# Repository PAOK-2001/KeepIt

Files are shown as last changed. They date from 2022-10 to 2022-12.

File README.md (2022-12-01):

# System Overview

The present system is intended as a demonstrator of how to apply computer vision techniques for autonomous driving. In particular, we tackle the matter of lane detection and following.

To deploy the image processing we will use a _Raspberry Pi 4B_ which will run the OpenCv script that finds the lanes and computes the center; it will also calculate the offset between said center and the center of the camera, returning an error (measured in pixels). The systems for moving and steering the car are controlled by a _Raspberry Pi Pico_, running FreeRTOS. The micro-controller will read the error by I2C and apply a proportional control loop (tunned using the Ziegler-Nichols experimental method) to correct the direction using the steering. 

Current and voltage sensors for a stable functioning of the system; a low-pass filter was implemented to rule out any current peaks and only stop the system when current to the motors consistently rises as a result of motor stall.

The system is summarized in the following diagram.

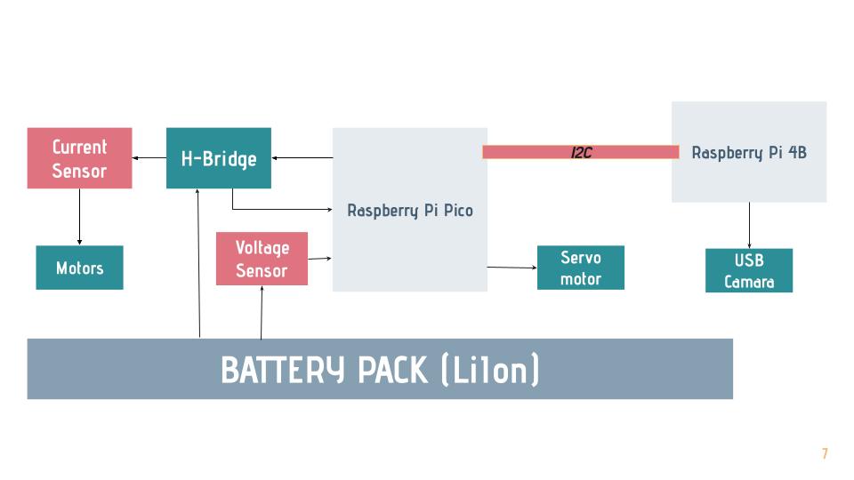
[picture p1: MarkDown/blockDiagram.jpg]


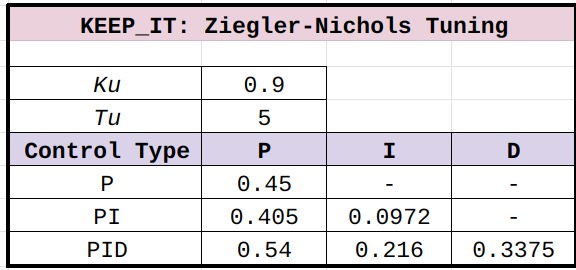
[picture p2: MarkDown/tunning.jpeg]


# Lane Detector
## Methodology
The focus of this project was to create a lane detector class for future implementation in lane keep. The approach for detecting the lanes consisted in finding the edges present in the image using gradient difference (Canny); then masking the image to only include the area corresponding to the road, upon which Hough Transform was applied, detecting probable lines in the image. A linear regression was obtained for each line, which allowed the classification into right (positive slope) and left (negative slope) boundaries; finally, the average coefficients  were found for each boundary, which described the average lines that delimited the lane.  

## Theoretical Background
### Hough Transform
Represents points as lines in Hough space, where the axis represents the values of a linear equation corresponding to a line that goes through that point . In particular, Hough transform uses the polar representation of a line      &rho;= Acos(&theta;)+Bcos(&theta;) where the axes are &rho; and &theta;.

For multiple points, Hough Transform detects the area in Hough space with the
most number of interceptions, returning the most probable values of the linear equation describing the collection of points. In OpenCV this is implemented as HoughLinesP, and returns the cartesian coordinates of the detected line in a vector of 4 integers Vec4i {x1,y1,x2,y1}.

Hough Space HoughTransform

### Canny Edge Detection

Canny is an algorithm that uses various states to detect the edge lines in an image. Firstly it applies a Gaussian Blur to the matrix of pixels to eliminate noise within the image. 
    
Then it uses the Sobel operator to calculate the pixel gradient in all directions. for those gradients Canny’s algorithm looks for those who are bigger than their neighbors, returning a thin edge line. 

## Lane Detector Object

    class laneDetector{
        private:
            // Images states used in lane detection
            Mat edgeImg, lineImg;
            // Lane lines in the format of a 4 integer vector such as  (x1, y1, x2, y2), 
            Vec4i leftLine, rightLine;
            // Coordinate that represents the senter of given lane
            Point center;
            // Auxiliary functions
            static pair<float,float> linearFit(Vec4i lineCoordinates); 
            static float averageCoheficient(vector<float> registeredCoheficients);
            static Vec4i makeCoordinate(float slope, float intercept, int imgHeight);

        public:
            laneDetector();
            void loadFrame(Mat cameraFrame);
            void findLanes();
            void findCenter();
            void display(Mat cameraFrame);
    };
### Class Composition
#### Atributes
| Atribute | Description |
| --- | ----- |
| edgeIMG | Pixel matrix that stores the Canny version of the loaded frame.Canny edgeIMG  |
| lineIMG | Pixel matrix that stores the drawed lines and center point that will blended with the orignal image in the final display. lineIMG edgeIMG |
| leftLine, rightLine | A Vec4i structure that stores the coordinates of the endpoints of the respective lines that delimit the lane. Format: {x1, y1, x2, y2}|
|center|Point object that stores the coordinates for the center of the lanes|
#### Methods
##### Static
|Method| Description  |
| --- | ----- |
|linearFit(Vec4i lineCoordinates)|Takes a vector of 4 integers representing the endpoints of a line and returns the slope and intercept as a pair.|
|averageCoheficient(vector<float> registeredCoheficients)|Takes a vector of coheficients and returns the average value.|
|makeCoordinate(float slope, float intercept, int imgHeight)|Takes the coheficients of a linear equation and the height of the image and calcultates the coordinates of a a line.|
##### Non-Static
|Method| Description  |
| --- | ----- |
|void loadFrame(Mat cameraFrame) | Loads the image where the lanes wish to be found. It applies converts it to grayscale, and applies Canny Edge Detection, storing the result in *edgeIMG*.|
|void findLanes()| It makes mask using polygons to isolate the area where the road is, updating *edgeIMG*. Once the region on interest is obtained Hough Transform is used to detect the lines present; afterwards the **linearFit** method is used to find the slope and intercept for each line. Based on the slope, the lines are categorized into right and left boundaries. Finally, it finds the average lines for each side using **averageCoheficient** and it makes the endpoint coordinates (using **makeCoordinates**) to store them in *rightLine* and *leftLine*. It draws said lines on *lineIMG*|
|void findCenter()|Finds the center of the lane using the coordinates stored in *rightLine* and *leftLine*. Draws the center as a circle in *lineIMG*|
|void display(Mat cameraFrame) | Overlays the *lineIMG* on the real fram captured by the camera. |

# Implementaion
The Lane Detector can be used to find lanes in a single image or a video (read from a file or camera.)

**Still image:**

    laneDetector lanes;
    frame = imread("imageName");
    lanes.loadFrame(frame);
    lanes.findLanes();
    lanes.findCenter();
    lanes.display(frame);

**Camera:**

    VideoCapture dashCam(path);
    for (;;){
        dashCam.read(frame);
        lanes.loadFrame(frame);
        lanes.findLanes();
        lanes.findCenter();
        lanes.display(frame);
        if(waitKey(5)== 27){
            break;
        }
    }

# CAD DESIGN

## Base and Steering

For this project we decided to laser cut a custom base to build the model car upon; we designed it using SolidWorks and leaving the necessary holes for mounting the electrical system. A custom shroud was also built to mount the web cam on the front of the car.

For controlling the direction of the model, we implemented a simplified version of _Ackermann Steering_ which is controlled using a servo motor. 

Finished prototype             | View of Ackermann Steering
:-------------------------:|:-------------------------:
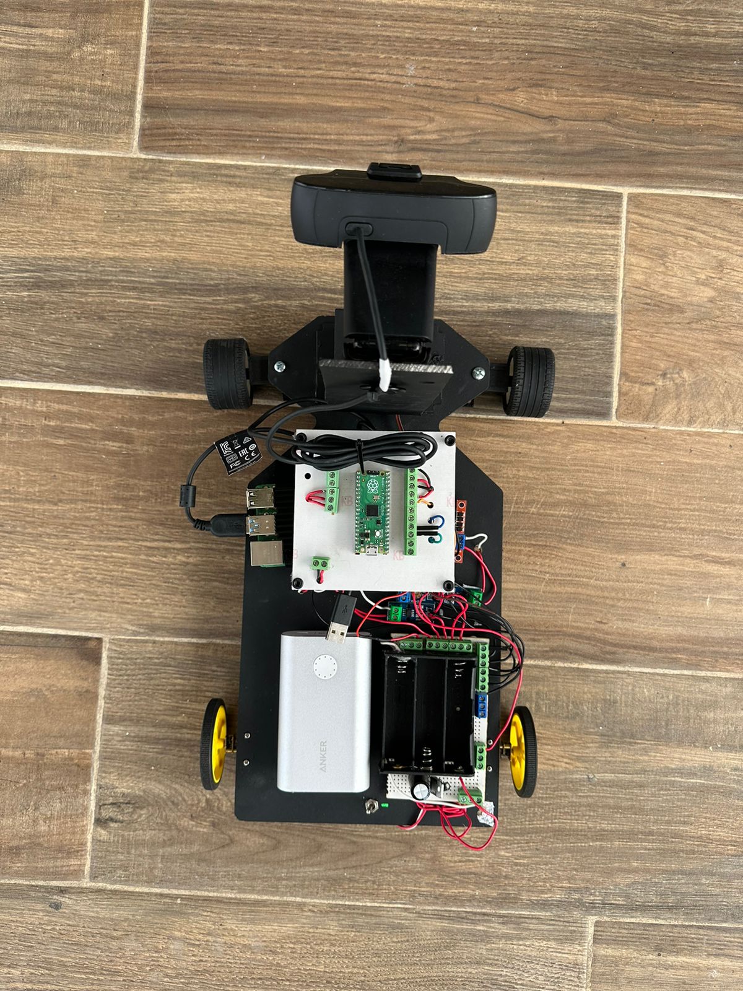
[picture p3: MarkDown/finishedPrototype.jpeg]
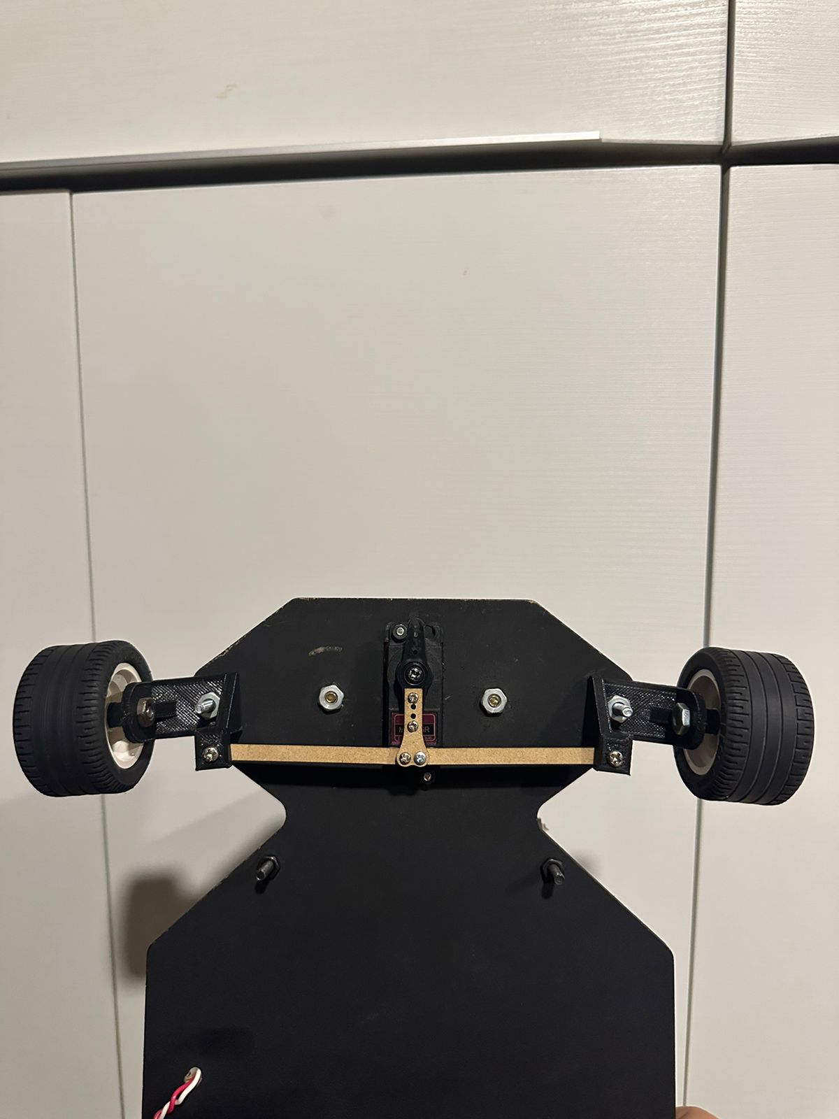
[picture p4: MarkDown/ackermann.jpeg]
  |   

## Electrical

For a secure connection a breakout board was made to map the GPIO pins using screw terminals. A power breakout board was also designed for a 4 cells 18650 BMS; however, due to a faulty BMS it was not used in the final implementation.
GPIO Breakout Board             | BMS Breakout Board
:-------------------------:|:-------------------------:
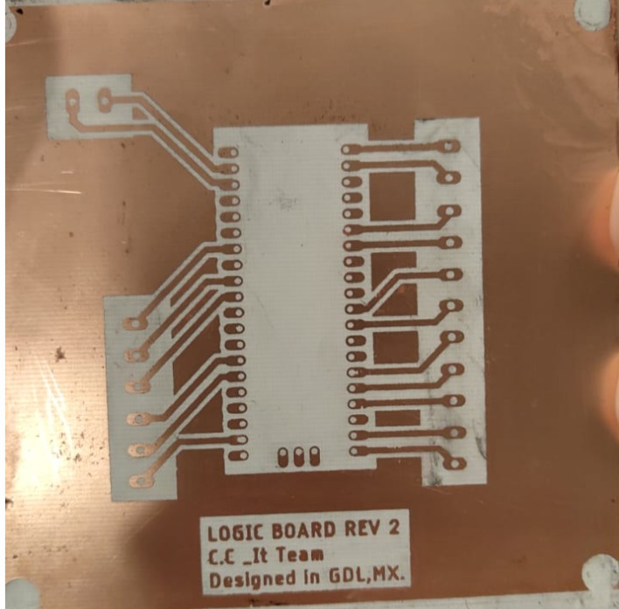
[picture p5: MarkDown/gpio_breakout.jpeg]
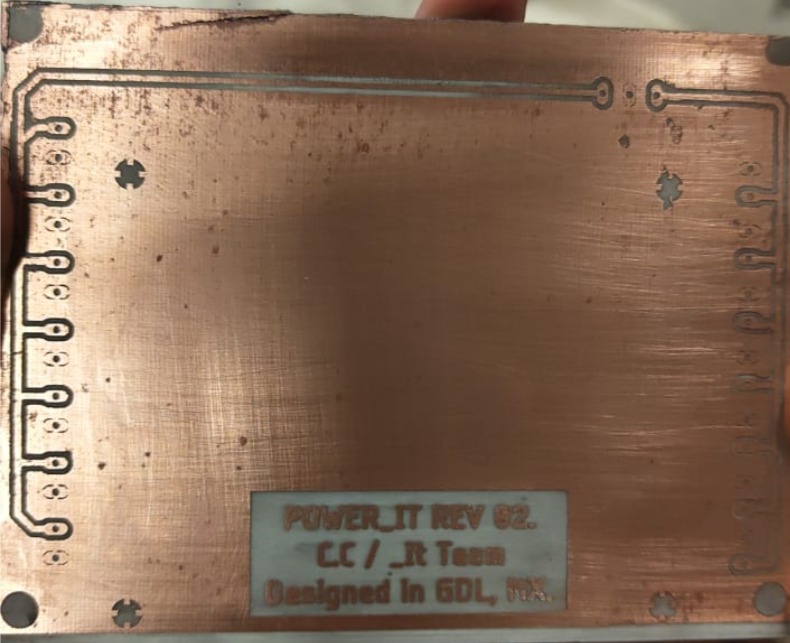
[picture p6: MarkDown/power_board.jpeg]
  |   

### Demo Reel: 

https://www.youtube.com/watch?v=GjENCYGIipA&ab_channel=AbrahamDeAlbaFranco

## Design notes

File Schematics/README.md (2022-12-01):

### Appendix: GPIO Breakout Board
_I2C0_
- GP4 (I2C0_SDA)
- GP5 (I2CO_SCL)

_I2C1_
- GP21 (I2C1_SDA)
- GP20(I2C1_SCL)
_UART COMMUNICATION_ 
- GP0
- GP1

_H-BRIDGE (PWM):_
- Motor1: GP15, GP14
- Motor2: GP13, GP12

_SERVO:_
- GP11

_ALIMENTATION_
- +:  VSYS [40]
- GND: [38]

_VOLTAGE SENSOR (ADC)_
- GP28

_CURRENT SENSORS (ADC)_
- SENSOR1: GP27
- SENSOR2: GP26

_GENERAL PURPOSE_:
- GP8
- G99
- GP17

### POWER

- 5V:  x7
- 3.3V: x7
- 12V: x3
- GND: x7

# Photos

_Acknowlegment:_ Special thanks to [John Corrado (@CorradoCorrado)](https://github.com/CorradoCorrado) for his guidance on the design and manufacturing of the boards!

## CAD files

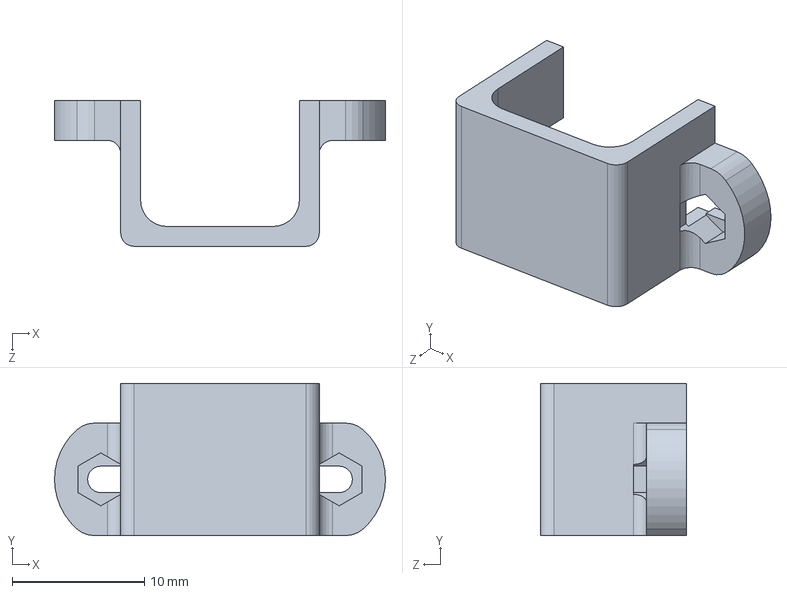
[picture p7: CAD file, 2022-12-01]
Schematics/Chassis_and_direction/Bracket.step.SLDPRT
25.0 x 11.5 x 11.0 mm

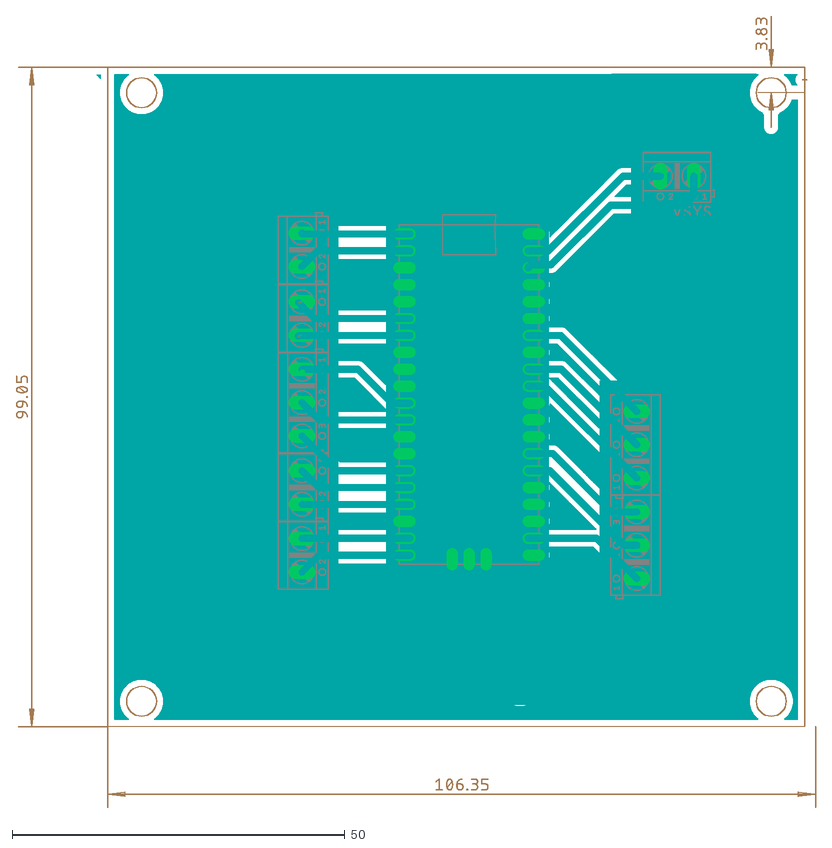
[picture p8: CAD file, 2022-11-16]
Schematics/LogicBoard - Pico/LogicBoard-Pico.dxf
120.2 x 118.9

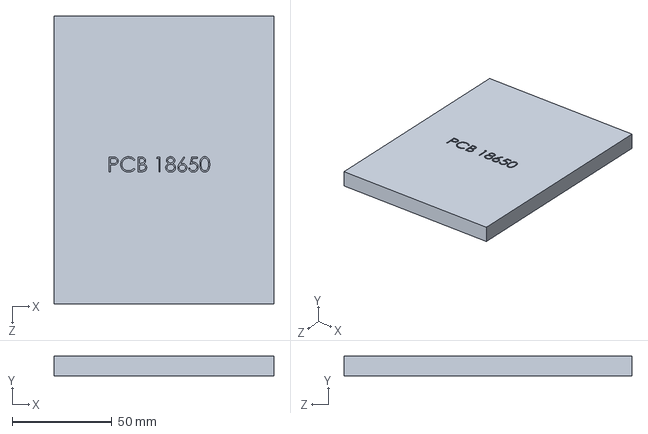
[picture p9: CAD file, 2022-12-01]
Schematics/Chassis_and_direction/bms.SLDPRT
110.0 x 10.0 x 144.0 mm

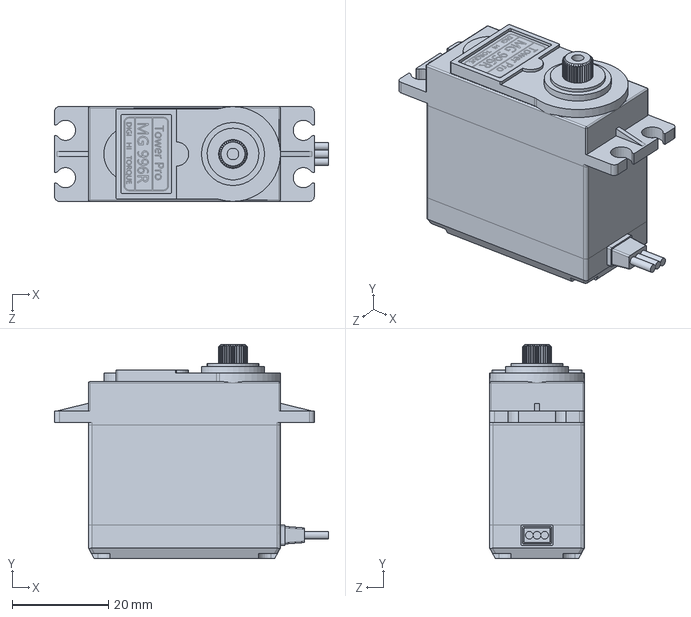
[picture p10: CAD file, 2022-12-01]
Schematics/Chassis_and_direction/Servo Motor MG996R.SLDPRT
57.0 x 44.5 x 19.7 mm

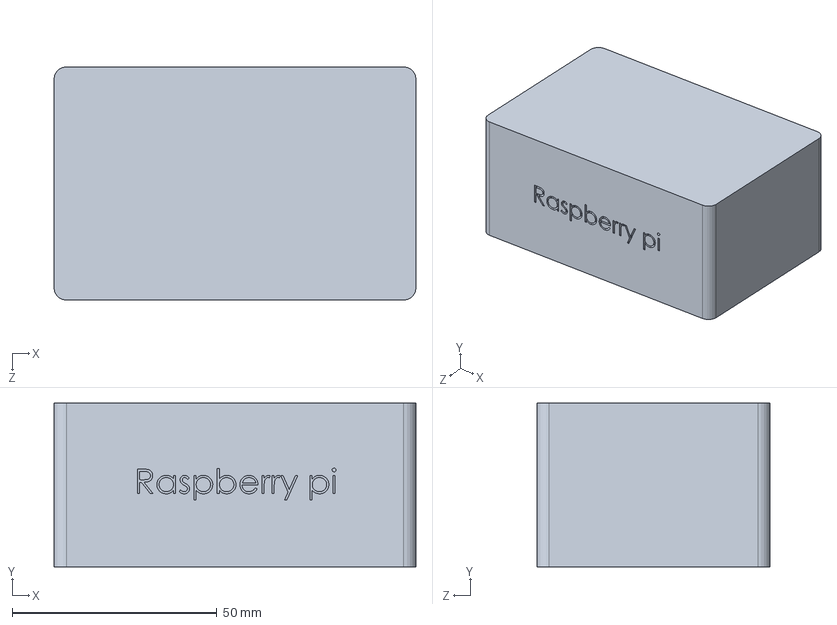
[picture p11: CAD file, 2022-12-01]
Schematics/Chassis_and_direction/Raspberry.SLDPRT
88.5 x 40.0 x 57.0 mm

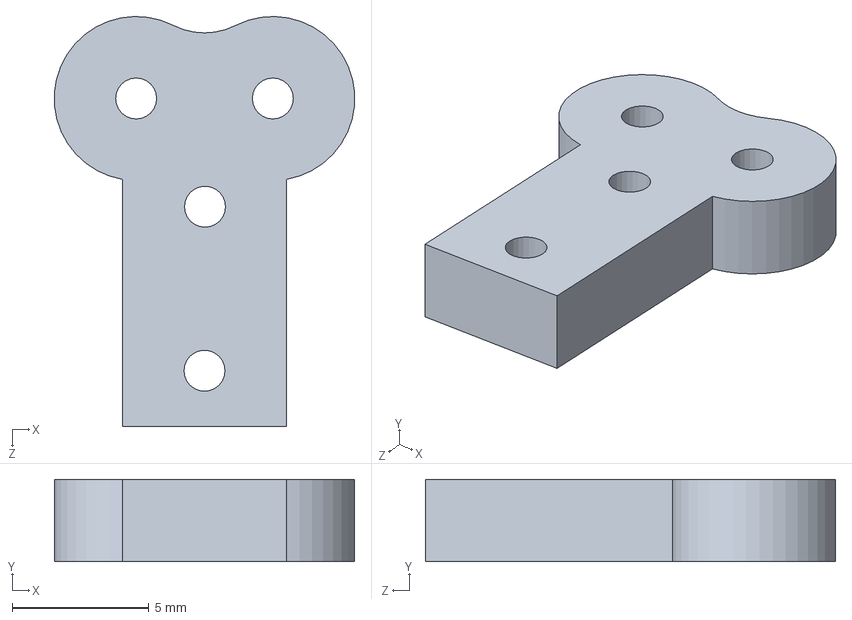
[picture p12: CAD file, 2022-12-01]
Schematics/Chassis_and_direction/linkage.SLDPRT
11.0 x 3.00 x 15.0 mm

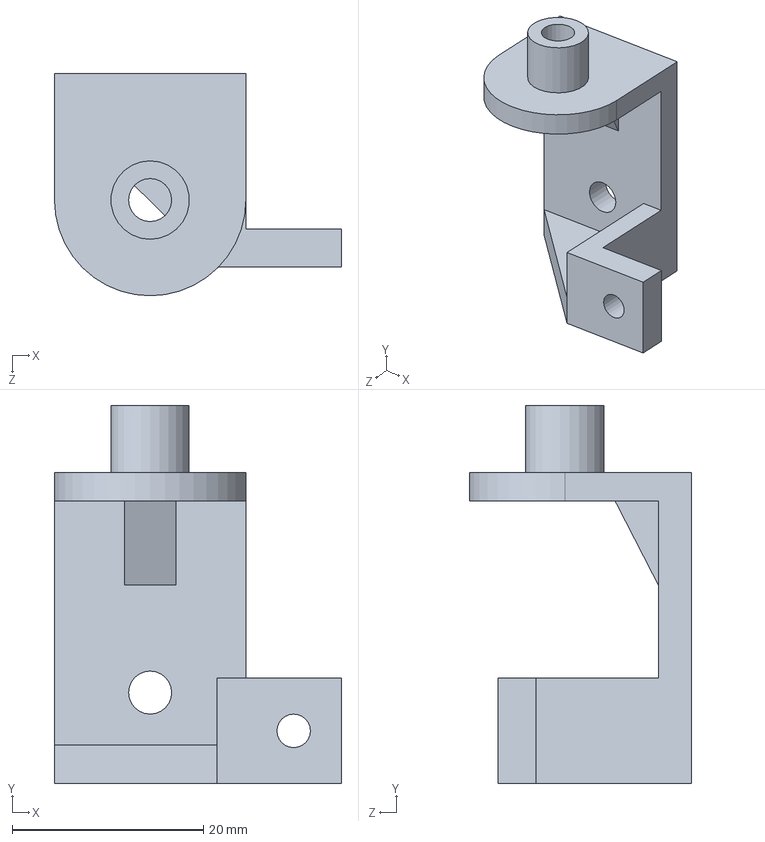
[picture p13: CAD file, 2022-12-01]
Schematics/Chassis_and_direction/Knuckle_R.SLDPRT
30.0 x 39.5 x 23.2 mm

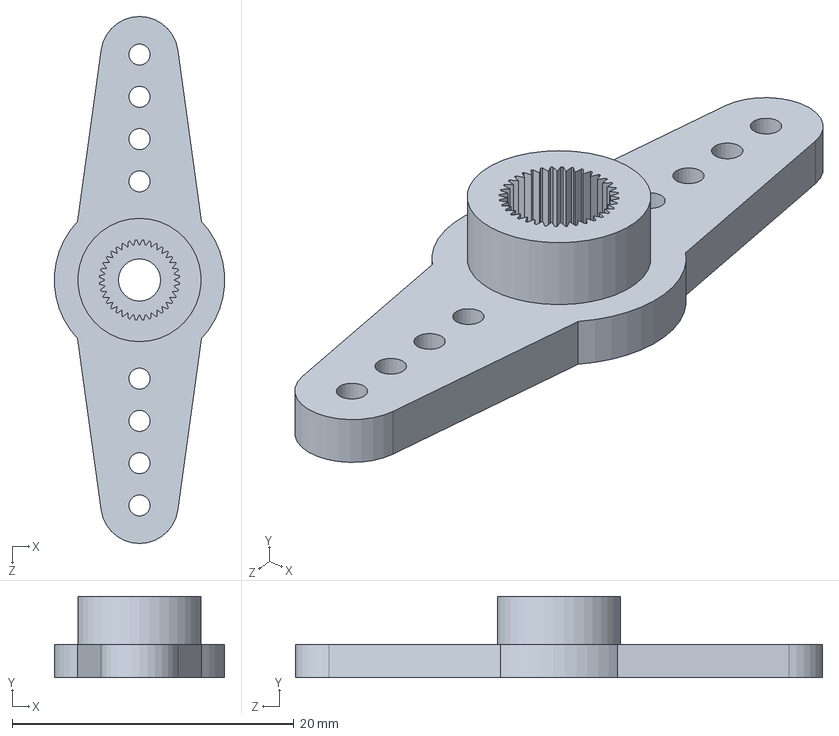
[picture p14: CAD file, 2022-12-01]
Schematics/Chassis_and_direction/Servo straight attachment.SLDPRT
12.1 x 5.75 x 37.4 mm

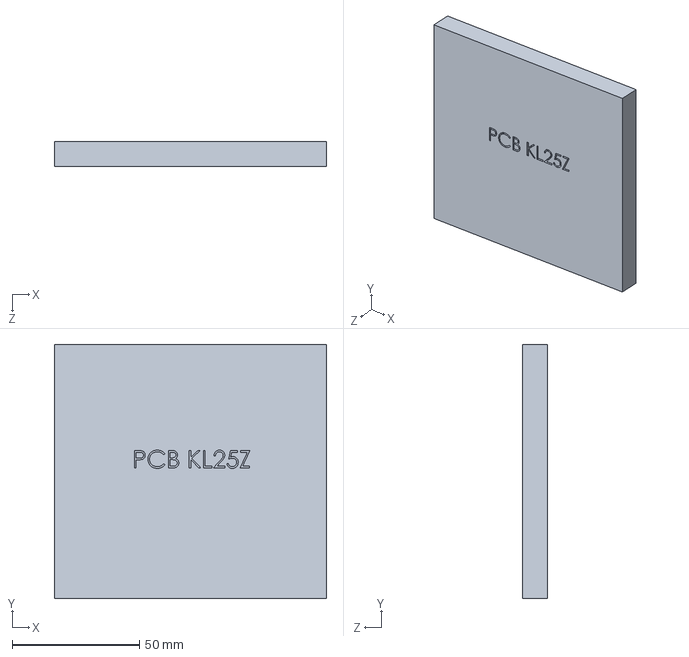
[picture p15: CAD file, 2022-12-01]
Schematics/Chassis_and_direction/pcb_kl25z.SLDPRT
107.0 x 100.0 x 10.0 mm

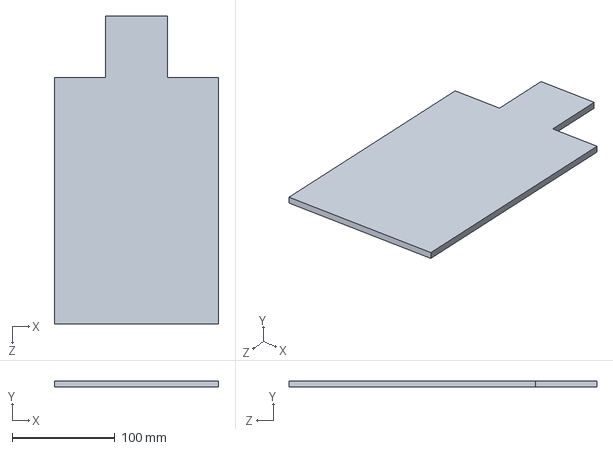
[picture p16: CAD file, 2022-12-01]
Schematics/Chassis_and_direction/Base.SLDPRT
160.0 x 6.00 x 300.0 mm

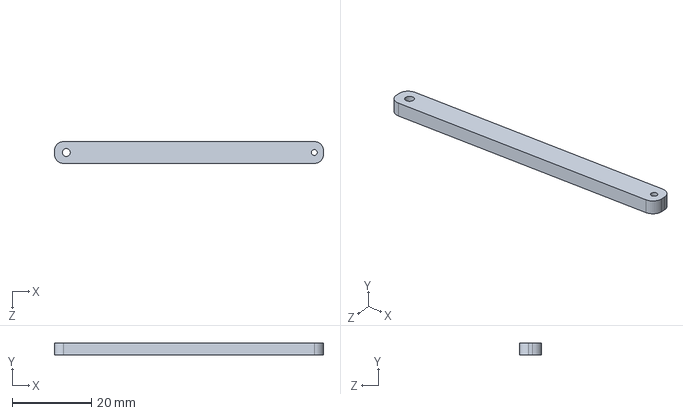
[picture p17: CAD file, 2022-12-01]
Schematics/Chassis_and_direction/side_linkage.SLDPRT
68.0 x 3.00 x 5.50 mm

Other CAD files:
Schematics/Chassis_and_direction/Knuckle_L.SLDPRT

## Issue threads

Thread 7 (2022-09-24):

Implement DSP error detection

PacoRmzA, 2022-09-24:

PAOK-2001, 2022-12-01:
@PacoRmzA  Designed lowpass filter in MATLAB using FIR1 method. And implemented in current sensor task

Closed 2022-12-01.

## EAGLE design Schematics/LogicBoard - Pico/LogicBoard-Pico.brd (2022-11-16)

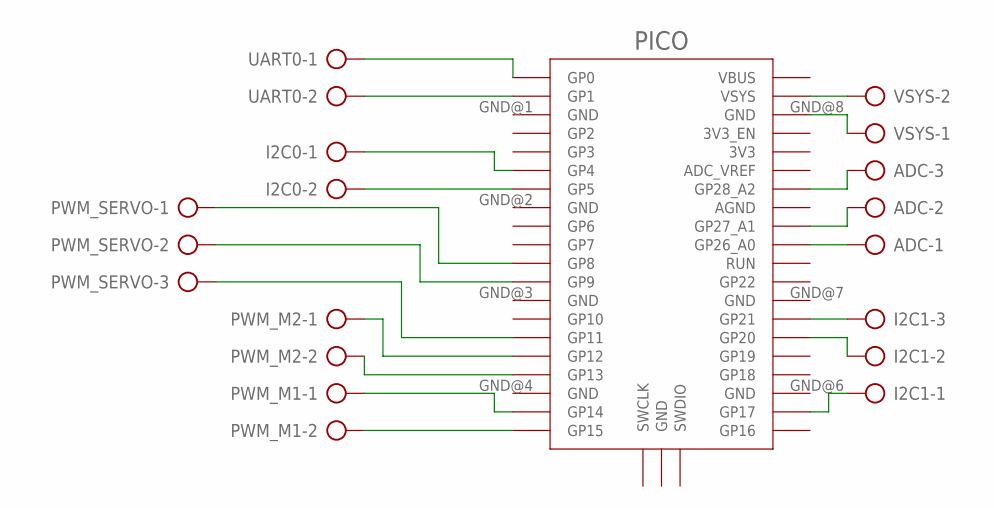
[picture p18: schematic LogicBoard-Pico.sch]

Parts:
ADC: AK500/3
I2C0: AK500/2
I2C1: AK500/3
PICO: RPI_PICO_IG-TH; RPI_PICO_TH
PWM_M1, PWM_M2: AK500/2
PWM_SERVO: AK500/3
UART0: AK500/2
VSYS: AK500/2

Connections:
unnamed: PICO.GND@8 (GND), VSYS.1
unnamed: PICO.VSYS, VSYS.2
unnamed: ADC.3, PICO.GP28_A2
unnamed: ADC.2, PICO.GP27_A1
unnamed: ADC.1, PICO.GP26_A0
unnamed: I2C1.3, PICO.GP21
unnamed: I2C1.2, PICO.GP20
unnamed: PICO.GP0, UART0.1
unnamed: PICO.GP1, UART0.2
unnamed: I2C0.1, PICO.GP4
unnamed: I2C0.2, PICO.GP5
unnamed: PICO.GP15, PWM_M1.2
unnamed: PICO.GP14, PWM_M1.1
unnamed: PICO.GP13, PWM_M2.2
unnamed: PICO.GP12, PWM_M2.1
unnamed: PICO.GP11, PWM_SERVO.3
unnamed: PICO.GP9, PWM_SERVO.2
unnamed: PICO.GP8, PWM_SERVO.1
unnamed: I2C1.1, PICO.GP17

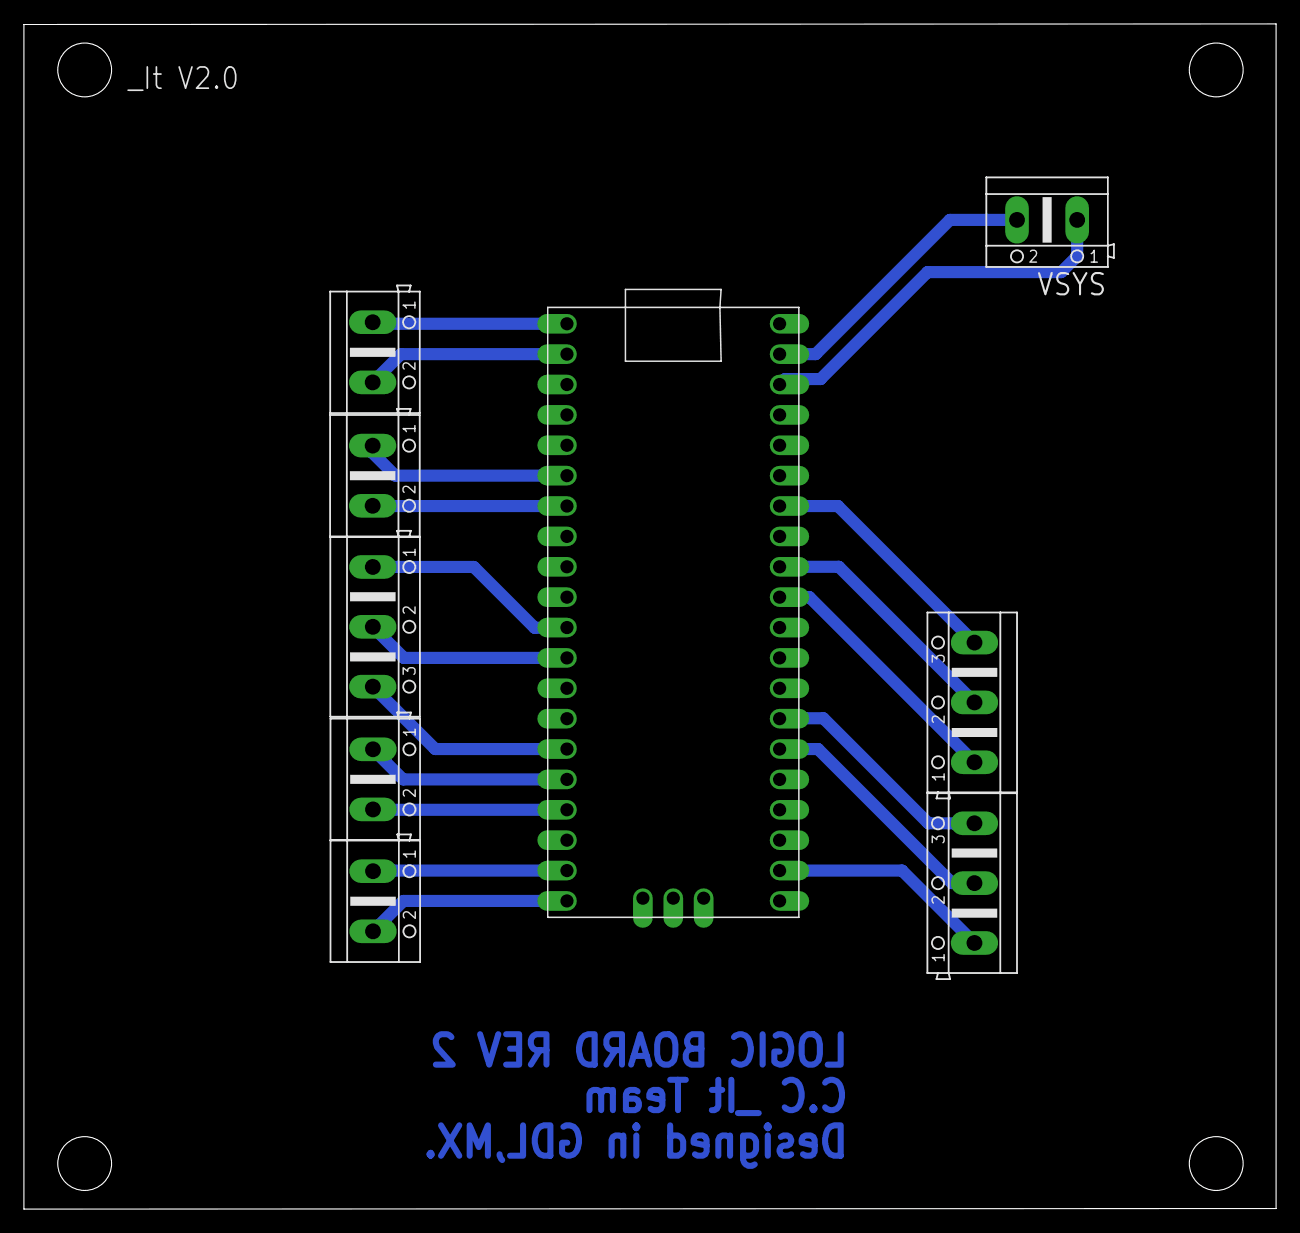
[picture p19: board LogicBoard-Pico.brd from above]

Board: 2 copper layers, 104.7 x 99.1 mm, 9 parts (0 on the bottom side), 19 nets.

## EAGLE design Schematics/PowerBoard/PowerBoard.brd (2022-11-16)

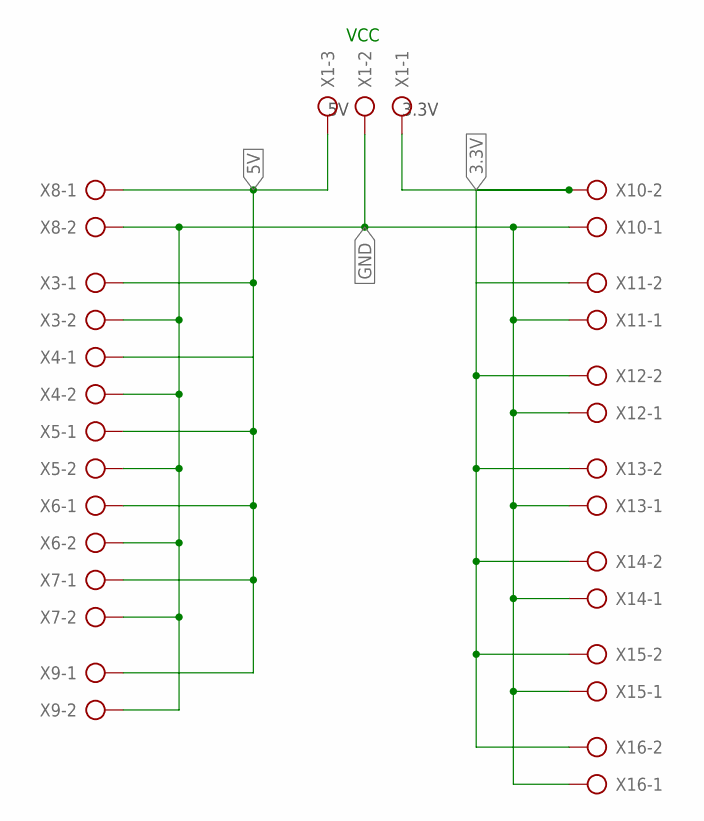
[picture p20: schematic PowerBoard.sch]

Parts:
X1: AK500/3
X3, X4, X5, X6, X7, X8, X9, X10, X11, X12, X13, X14, X15, X16: AK500/2

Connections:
3.3V: X1.1, X10.2, X11.2, X12.2, X13.2, X14.2, X15.2, X16.2
5V: X1.3, X3.1, X4.1, X5.1, X6.1, X7.1, X8.1, X9.1
GND: X1.2, X3.2, X4.2, X5.2, X6.2, X7.2, X8.2, X9.2, X10.1, X11.1, X12.1, X13.1, X14.1, X15.1, X16.1

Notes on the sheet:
VCC
3.3V

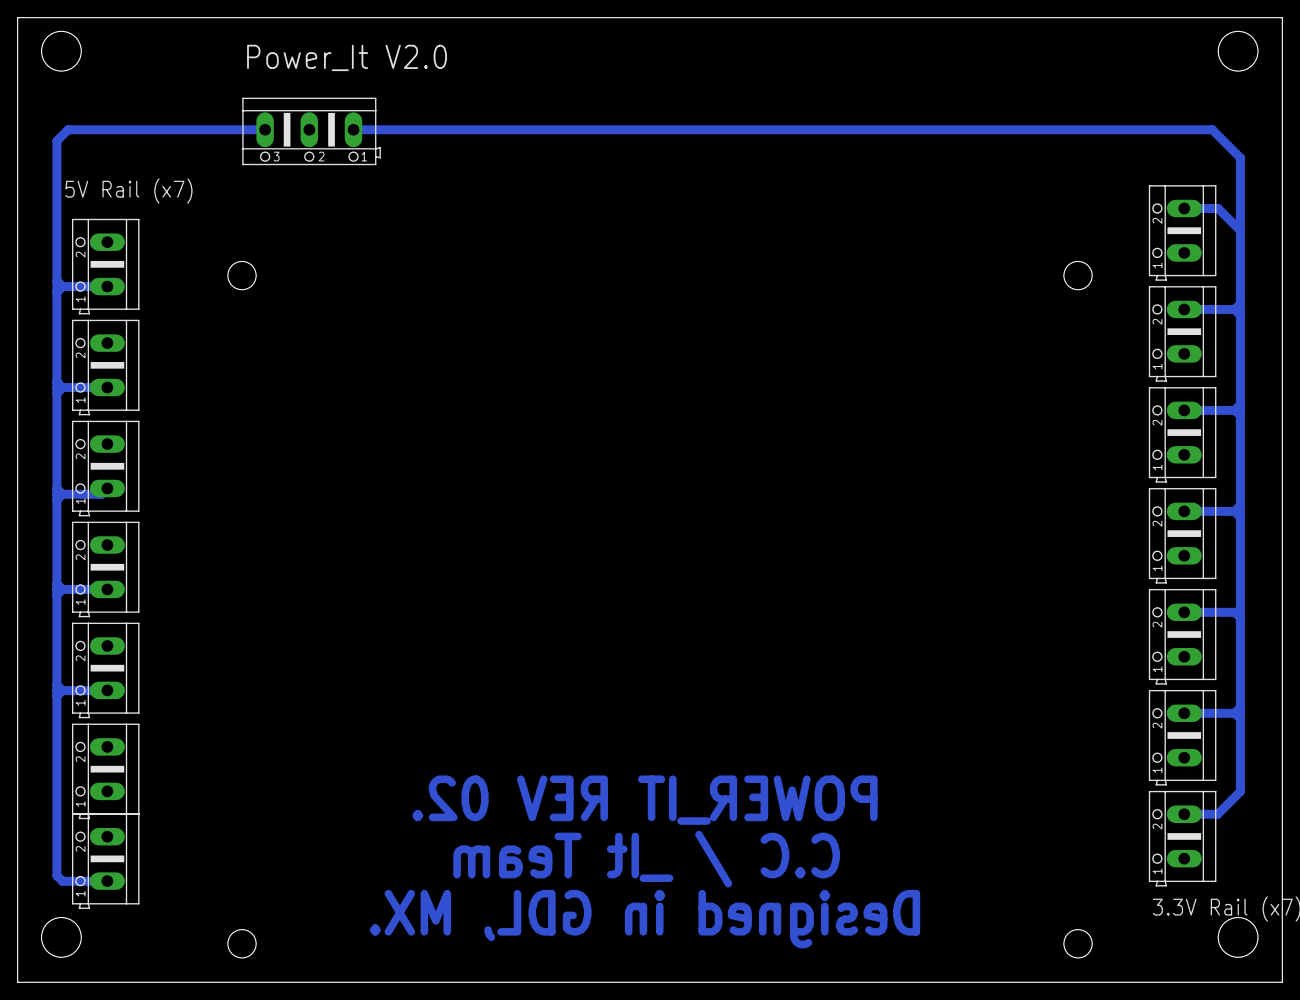
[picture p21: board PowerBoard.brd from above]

Board: 2 copper layers, 143.2 x 109.2 mm, 15 parts (0 on the bottom side), 3 nets.

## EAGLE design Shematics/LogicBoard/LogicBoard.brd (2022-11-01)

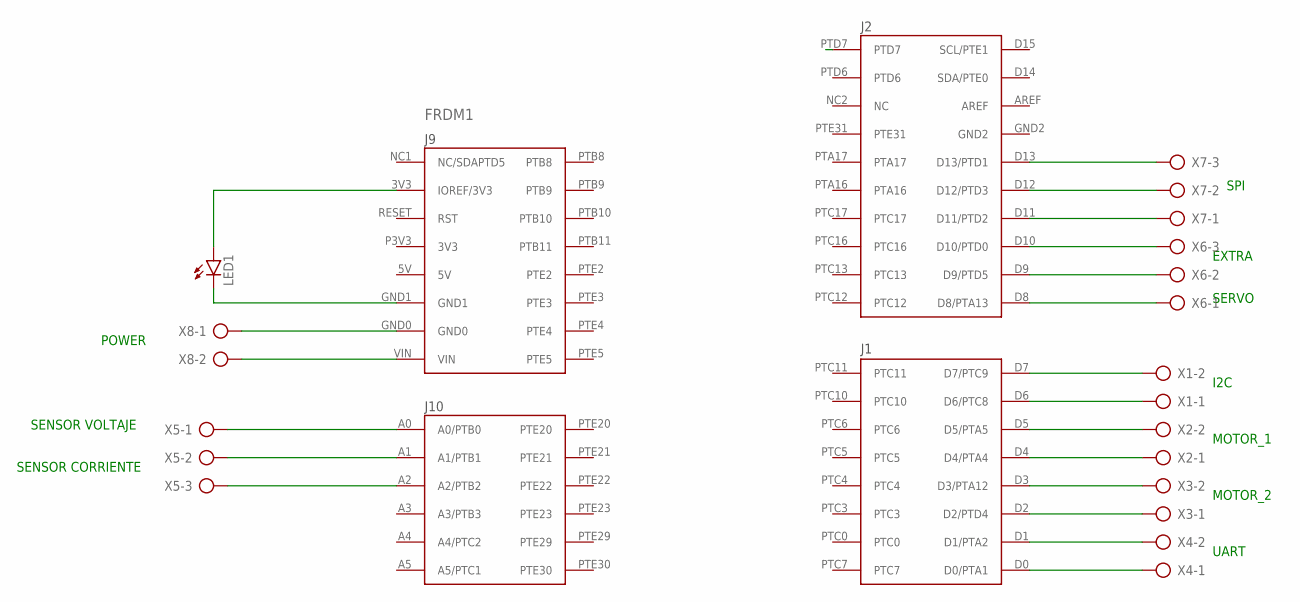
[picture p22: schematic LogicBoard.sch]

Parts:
FRDM1: FRDM-KL25ZNORMAL; FRDM_KL25Z_NORMAL
LED1: LED5MM
X1, X2, X3, X4, X8: AK500/2
X5, X6, X7: AK500/3

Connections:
unnamed: FRDM1.D7 (D7/PTC9), X1.2
unnamed: FRDM1.D6 (D6/PTC8), X1.1
unnamed: FRDM1.D5 (D5/PTA5), X2.2
unnamed: FRDM1.D4 (D4/PTA4), X2.1
unnamed: FRDM1.D3 (D3/PTA12), X3.2
unnamed: FRDM1.D2 (D2/PTD4), X3.1
unnamed: FRDM1.D1 (D1/PTA2), X4.2
unnamed: FRDM1.D0 (D0/PTA1), X4.1
unnamed: FRDM1.GND0, X8.1
unnamed: FRDM1.VIN, X8.2
unnamed: FRDM1.A0 (A0/PTB0), X5.1
unnamed: FRDM1.A1 (A1/PTB1), X5.2
unnamed: FRDM1.A2 (A2/PTB2), X5.3
unnamed: FRDM1.D8 (D8/PTA13), X6.1
unnamed: FRDM1.D9 (D9/PTD5), X6.2
unnamed: FRDM1.D10 (D10/PTD0), X6.3
unnamed: FRDM1.D11 (D11/PTD2), X7.1
unnamed: FRDM1.D12 (D12/PTD3), X7.2
unnamed: FRDM1.D13 (D13/PTD1), X7.3
unnamed: FRDM1.GND1, LED1.K (C)
unnamed: FRDM1.3V3 (IOREF/3V3), LED1.A

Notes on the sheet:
I2C
UART
MOTOR_1
MOTOR_2
POWER
SENSOR VOLTAJE
SENSOR CORRIENTE
SERVO
EXTRA
SPI

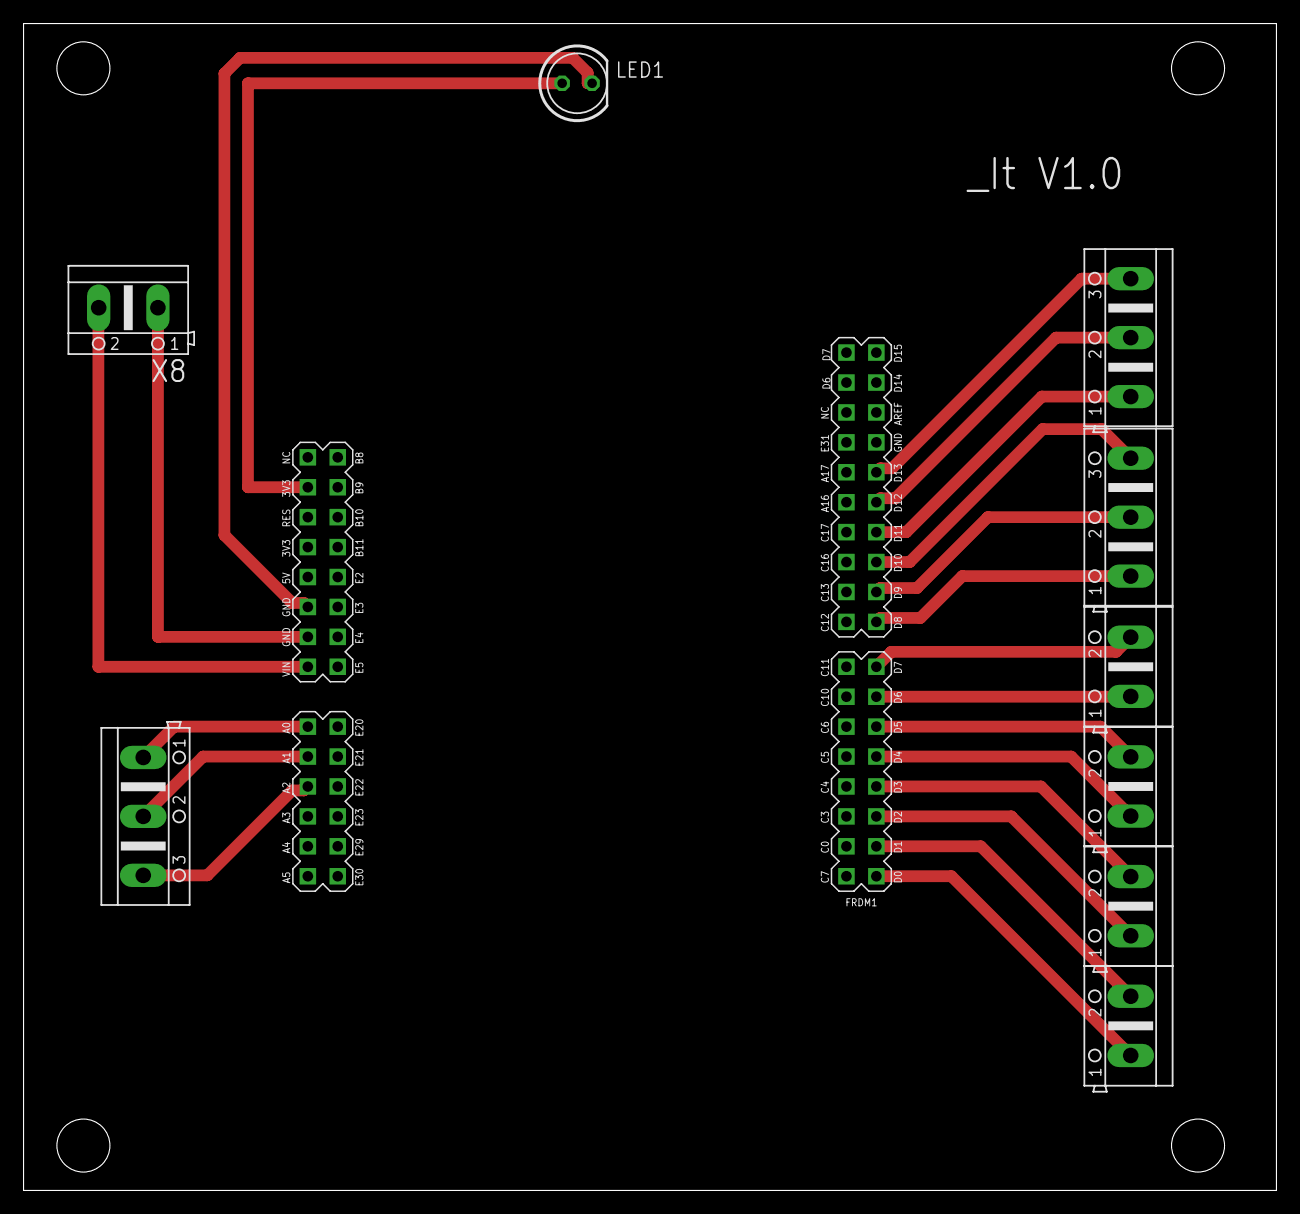
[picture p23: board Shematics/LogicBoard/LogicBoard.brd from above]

Board: 2 copper layers, 106.3 x 99.0 mm, 10 parts (0 on the bottom side), 21 nets.

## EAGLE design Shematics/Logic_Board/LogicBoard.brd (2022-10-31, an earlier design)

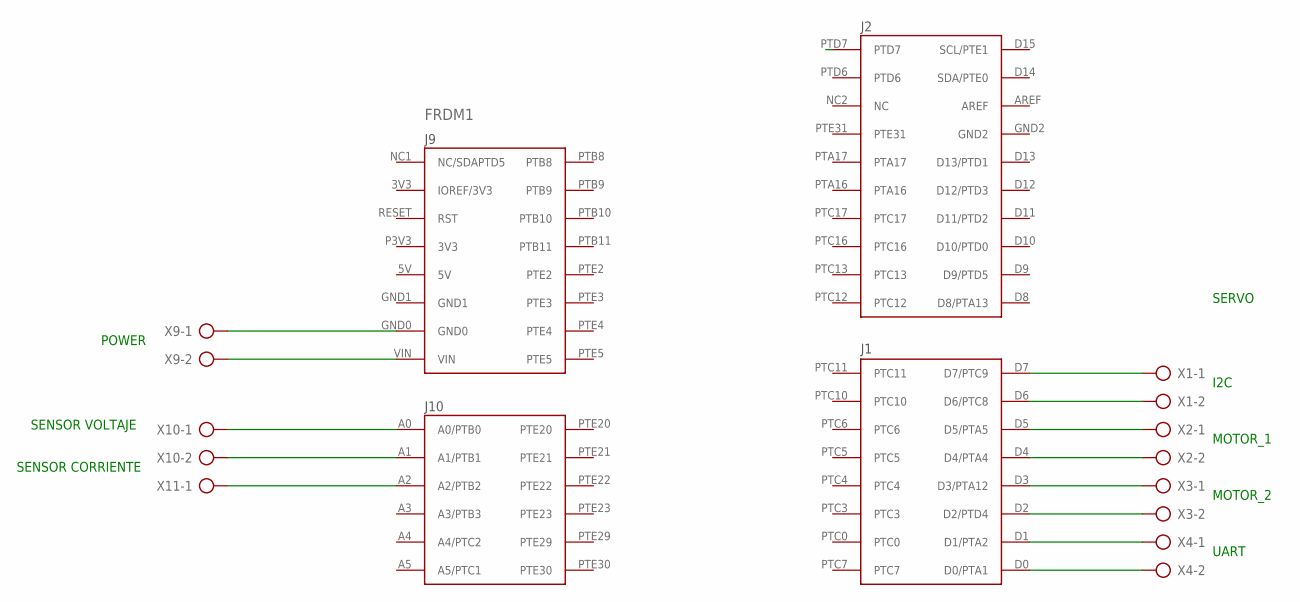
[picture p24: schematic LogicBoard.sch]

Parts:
FRDM1: FRDM-KL25ZNORMAL; FRDM_KL25Z_NORMAL
X1, X2, X3, X4, X9, X10, X11: AK500/2-H

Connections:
unnamed: FRDM1.D7 (D7/PTC9), X1.1
unnamed: FRDM1.D6 (D6/PTC8), X1.2
unnamed: FRDM1.D5 (D5/PTA5), X2.1
unnamed: FRDM1.D4 (D4/PTA4), X2.2
unnamed: FRDM1.D3 (D3/PTA12), X3.1
unnamed: FRDM1.D2 (D2/PTD4), X3.2
unnamed: FRDM1.D1 (D1/PTA2), X4.1
unnamed: FRDM1.D0 (D0/PTA1), X4.2
unnamed: FRDM1.VIN, X9.2
unnamed: FRDM1.GND0, X9.1
unnamed: FRDM1.A0 (A0/PTB0), X10.1
unnamed: FRDM1.A1 (A1/PTB1), X10.2
unnamed: FRDM1.A2 (A2/PTB2), X11.1

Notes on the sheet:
I2C
UART
MOTOR_1
MOTOR_2
POWER
SENSOR VOLTAJE
SENSOR CORRIENTE
SERVO

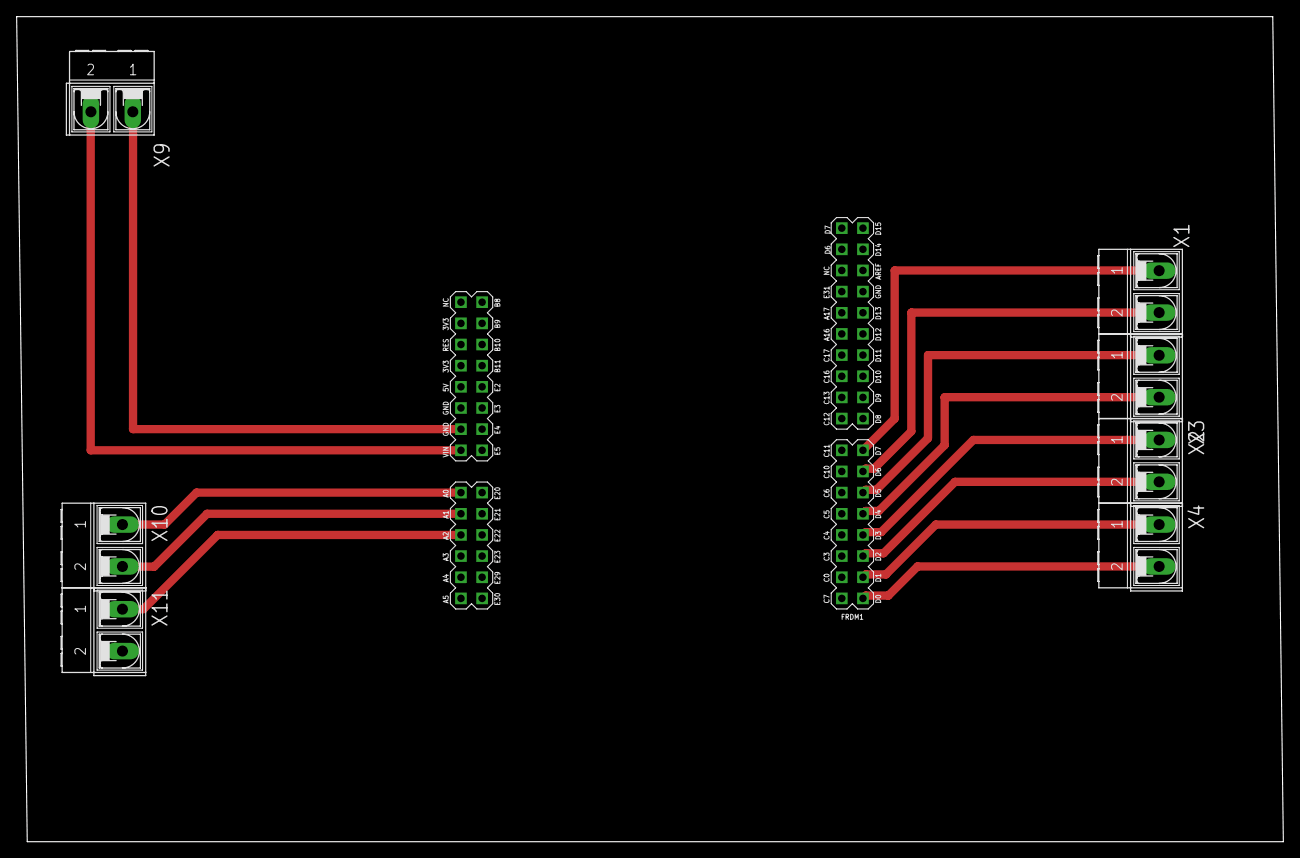
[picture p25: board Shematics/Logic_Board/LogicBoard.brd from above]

Board: 2 copper layers, 152.1 x 99.0 mm, 8 parts (0 on the bottom side), 13 nets.

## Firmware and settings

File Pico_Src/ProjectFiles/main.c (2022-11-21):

#include <stdio.h>
#include "pico/stdlib.h"
#include "hardware/i2c.h"
#include <FreeRTOS.h>
#include <task.h>
#include "headers/rtos_tasks.h"
#include "hardware/clocks.h"
#define PIN_OUT 0

int main(){
    stdio_init_all();
    xTaskCreate(i2c_task, "I2C_Task", 256, NULL, 5, NULL);
    xTaskCreate(control_task, "Control_Task", 256, NULL, 5, NULL);
    xTaskCreate(motors_task, "Motors_Task", 256, NULL, 4, NULL);
    //xTaskCreate(sensors_task, "Sensors_Task", 256, NULL, 2, NULL);
    vTaskStartScheduler();
   
}

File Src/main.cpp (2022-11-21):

// Lane Detector
#include "laneDetector.cpp"
#include <bits/stdc++.h>
#include "opencv2/core.hpp"
#include "opencv2/highgui/highgui.hpp"
#include "opencv2/imgproc.hpp"
#include "opencv2/imgcodecs.hpp"
#include <wiringPi.h>
#include <wiringPiI2C.h>

#define PICO_ADDR 0x0a
using namespace std;
using namespace cv;

int main(){
    int Com2Pico = wiringPiI2CSetup(PICO_ADDR);
    if (Com2Pico == -1) {
        cerr << "Failed to intialize communication with Pico.\n";
        return -1;
    }
    cout << "Communication with PIco successfully setup.\n";

    laneDetector lanes;
    Mat frame;
    VideoCapture dashCam(0);
    dashCam.set(CAP_PROP_FPS,15);
    dashCam.set(CAP_PROP_FRAME_WIDTH,640);
    dashCam.set(CAP_PROP_FRAME_HEIGHT,480);
    // Check if the dashCam is readable
    if(!dashCam.isOpened()){
        cout<<"Error reading dashCam feed\n";
        return -1;
    }
    int counter = 0;

    for (;;){
        dashCam.read(frame);
        // Check if selected source is sending information
        if(frame.empty()){
            cout<<"NULL frame ";
            break;
        }
        // Load image into lane detector
        lanes.loadFrame(frame);
        // Find lanes on given frame
        lanes.findLanes();
        // Find center of previously calculated lanes
        if(lanes.findCenter().x > 0 && lanes.findCenter().x < dashCam.get(CAP_PROP_FRAME_WIDTH) ){
            float reference = lanes.findCenter().x-dashCam.get(CAP_PROP_FRAME_WIDTH)/2.0;
            wiringPiI2CWriteReg16 (Com2Pico, 0x01, reference);
	    cout << reference << endl;
        }
        // Overlap lanes on the video
        //lanes.display(frame);
        // Wait 1 miliseconds
        // Read key board input, setting esc as break key
        if(waitKey(1)== 27){
            break;
        }
    }
    return 0;
}

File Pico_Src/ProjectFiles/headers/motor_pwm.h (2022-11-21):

#ifndef MOTOR_PWM_H
#define MOTOR_PWM_H

#include "pico/stdlib.h"
#include "hardware/clocks.h"
#include "hardware/pwm.h"

#define SERVO_PIN 11
#define SERVO_WRAP 9804
#define SERVO_MAX_LEFT 620   //Servo at -10°
#define SERVO_CENTER 715     //Servo at 0°
#define SERVO_MAX_RIGHT 799  //Servo at +10°

#define MOTOR_PWM_PERIOD 10000
#define MAX_SPEED MOTOR_PWM_PERIOD*0.8

#define MOTOR_OUTPUT_PIN_R1 12
#define MOTOR_OUTPUT_PIN_R2 13

#define MOTOR_OUTPUT_PIN_L1 14
#define MOTOR_OUTPUT_PIN_L2 15


int servo_slice, servo_channel;
int slice_num_R1, R1;
int slice_num_L1, L1;


void servo_init(){
    servo_slice   = pwm_gpio_to_slice_num(SERVO_PIN);
    servo_channel = pwm_gpio_to_channel(SERVO_PIN);
    gpio_set_function(SERVO_PIN, GPIO_FUNC_PWM); // Set the pin 0 to be PWM
    pwm_set_clkdiv(servo_slice, 256.0f);    // Setting the divider to slow down the clock
    pwm_set_wrap(servo_slice, SERVO_WRAP);  // setting the Wrap time to 9764 (20 ms)
    pwm_set_enabled(servo_slice, true);
    pwm_set_chan_level(servo_slice, servo_channel, SERVO_CENTER);

}

void motors_init() {
    gpio_set_function(MOTOR_OUTPUT_PIN_R1, GPIO_FUNC_PWM);
    gpio_set_function(MOTOR_OUTPUT_PIN_L1, GPIO_FUNC_PWM);

    int R1 = pwm_gpio_to_channel(MOTOR_OUTPUT_PIN_R1);
    int L1 = pwm_gpio_to_channel(MOTOR_OUTPUT_PIN_L1);

    slice_num_R1 = pwm_gpio_to_slice_num(MOTOR_OUTPUT_PIN_R1);
    slice_num_L1 = pwm_gpio_to_slice_num(MOTOR_OUTPUT_PIN_L1);

    pwm_set_clkdiv(slice_num_R1, 256.0f); 
    pwm_set_clkdiv(slice_num_L1, 256.0f); 

    pwm_set_wrap(slice_num_R1, MOTOR_PWM_PERIOD);
    pwm_set_wrap(slice_num_L1, MOTOR_PWM_PERIOD);

    pwm_set_chan_level(slice_num_R1, R1, MOTOR_PWM_PERIOD);
    pwm_set_enabled(slice_num_R1, true);
    if (slice_num_R1 != slice_num_L1) {
        pwm_set_chan_level(slice_num_L1, L1, MOTOR_PWM_PERIOD);
        pwm_set_enabled(slice_num_L1, true);
    }

}

void servo_write(uint period){
    if(period >= SERVO_MAX_RIGHT){
        pwm_set_chan_level(servo_slice, servo_channel, SERVO_MAX_RIGHT);
    }
    else if(period <= SERVO_MAX_LEFT){
        pwm_set_chan_level(servo_slice, servo_channel, SERVO_MAX_LEFT);
    }else{
        pwm_set_chan_level(servo_slice, servo_channel, period);  /// Setting the duty period (0.6 ms)
    }
}

void servo_180_sweep(){
    for (uint i = SERVO_MAX_LEFT; i < SERVO_MAX_RIGHT; i+=40)
    {
        pwm_set_chan_level(servo_slice, servo_channel, i);  /// Setting the duty period (0.6 ms)
        sleep_ms(1500);
    }
}

void motors_forward(int speed){
    pwm_set_chan_level(slice_num_R1,R1,speed);
    pwm_set_chan_level(slice_num_L1,L1,speed);
}

#endif

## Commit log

2022-09-28 Removed mask and change feed from video to camera
2022-09-28 Removed sample videos
2022-09-29 Framerate and resolution change
2022-10-01 Added color filtering and slope discrimination
2022-10-31 Added board schematic
    [LogicBoard.brd, LogicBoard.sch]
2022-11-01 Refactored logic board & completed power distribution board
    [LogicBoard.brd, LogicBoard.sch, PowerBoard.brd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]
2022-11-10 Updated Schematics
    [LogicBoard-Pico.brd, LogicBoard-Pico.sch, LogicBoard.brd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]
2022-11-10 Created Pico project template
2022-11-10 First Rasp Pico compilation attempt
2022-11-11 Pico build attempt #2 (seems to work)
2022-11-11 Implemented FreeRTOS file structure
    [LogicBoard-Pico.brd, LogicBoard-Pico.sch, LogicBoard.brd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]
2022-11-11 First draft of I2C communication
2022-11-11 Implemented basic motor and servo tasks
2022-11-12 Testing I2C
2022-11-13 Implemented setup in I2C task
2022-11-14 Finished initial I2C setup in rtos task
2022-11-14 Implemented read error from Raspberry Pi 4B, over I2C.
    [rtos_tasks.h]
2022-11-14 Send lane error to Pico with I2C
    [main.cpp]
2022-11-16 Refactored Power PCB
    [LogicBoard-Pico.brd, LogicBoard.brd, LogicBoard.sch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]
2022-11-16 Refactored logic board
    [LogicBoard-Pico.brd, LogicBoard-Pico.dxf]
2022-11-19 Servo draft
2022-11-19 Added PWM control for drivetrain, Tuned servo limits
2022-11-21 Added fail safe to avoid system exeeceding limits
    [motor_pwm.h]
2022-11-21 Added prints for debugging purposes
2022-11-21 Changed servo left limit and added an isReceiving flag
2022-11-22 Implemented DSP filter and current overload handle
2022-11-30 Added 3D design files
    [Base.SLDPRT, Bracket.step.SLDPRT, Knuckle_L.SLDPRT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]
